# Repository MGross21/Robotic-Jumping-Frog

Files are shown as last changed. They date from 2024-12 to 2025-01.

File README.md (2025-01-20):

# Robotic Jumping Frog
*A Bio-Inspired Robotic System Aimed to Compare Physics Simulation and Physical Recreation*

*By Jacob Pisors and Michael Gross*

## Video Presentation

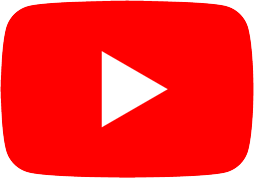
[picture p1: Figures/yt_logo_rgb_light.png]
See Here (https://www.youtube.com/embed/GysCEJ6NQpc)

\
`Click YouTube Logo to be Redirected`

## Project Overview

Continuing with the project's previous research, the team hopes to define the frog five-bar model in simulation using Mujoco, building off the kinematics. Then optimize the parameters for design, namely the joint stiffness, overall length, and various link lengths. Given this, the team will plan and fabricate the prototype using foldable robotics methods, and use then test it and capture the results. With that, an experimental validation will be complete and the team can analyze the results.

Specifically, the scope of this project is given the frog's inherent body mass, how can we reconfigure the link lengths and material stiffness of the five-bar mechanism, representative of rear frog legs, to determine the optimal vertical and horizontal propulsion during its jumping gait. The rationale for this decision is explained in part 2, where we optimized the design.

Simulation vs Prototype Final Video Results
___

### Part 1: Define the System Model

The model, as linked [here](frogModel.xml), allows for link lengths and joint stiffness to be changed easily by passing in the desired lengths. This will update the model and help when re-running the simulation many times as needed for optimization.

The team used [motor characterization](System_Model_Identification/MotorModel.ipynb) and [compliant beam analysis](System_Model_Identification/compliant_beam_analysis.ipynb) to determine the model parameters. 

Additionally in this step, considering the desire for a two-foot jumping gait, the team determined through the motor motor characterization and analysis that there was a physical constraint to the design of the controller and the max potential impulse. The minimum time in which we could use the full 180-degree motion of the servo was about 0.35 seconds which not only determined how fast the legs could move but how fast they could retract before landing.

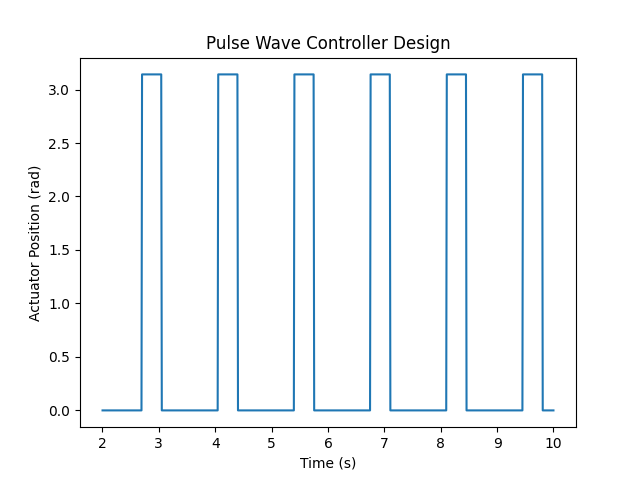
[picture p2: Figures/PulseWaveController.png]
PulseWaveController


___

### Part 2: Optimize your Design

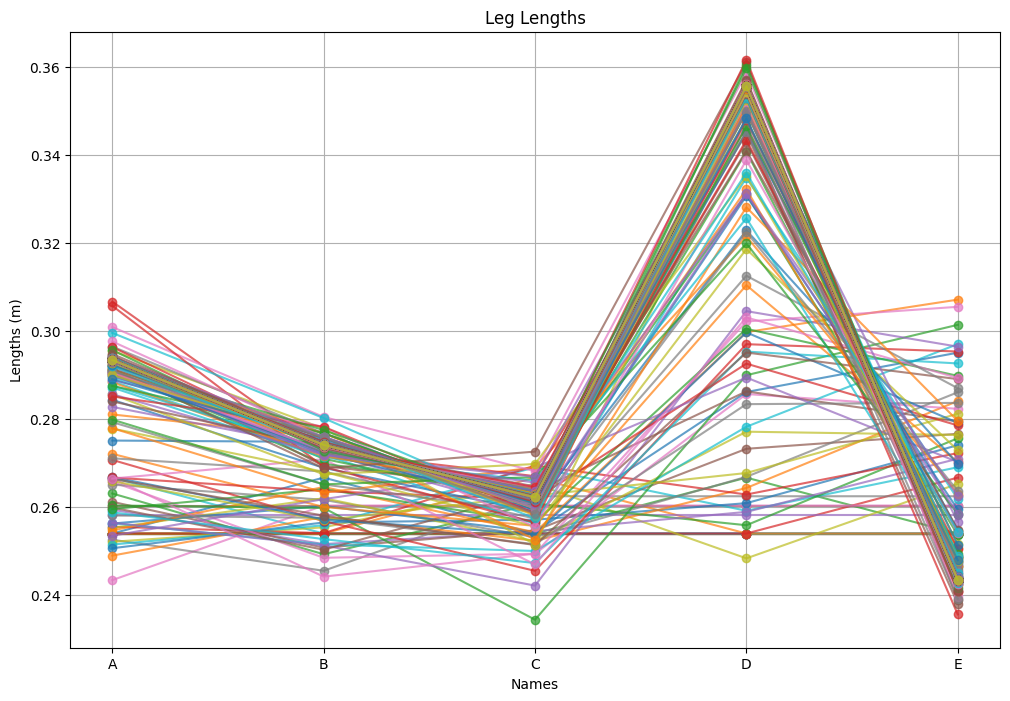
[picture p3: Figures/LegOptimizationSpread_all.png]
LegOptimizationSpread_all


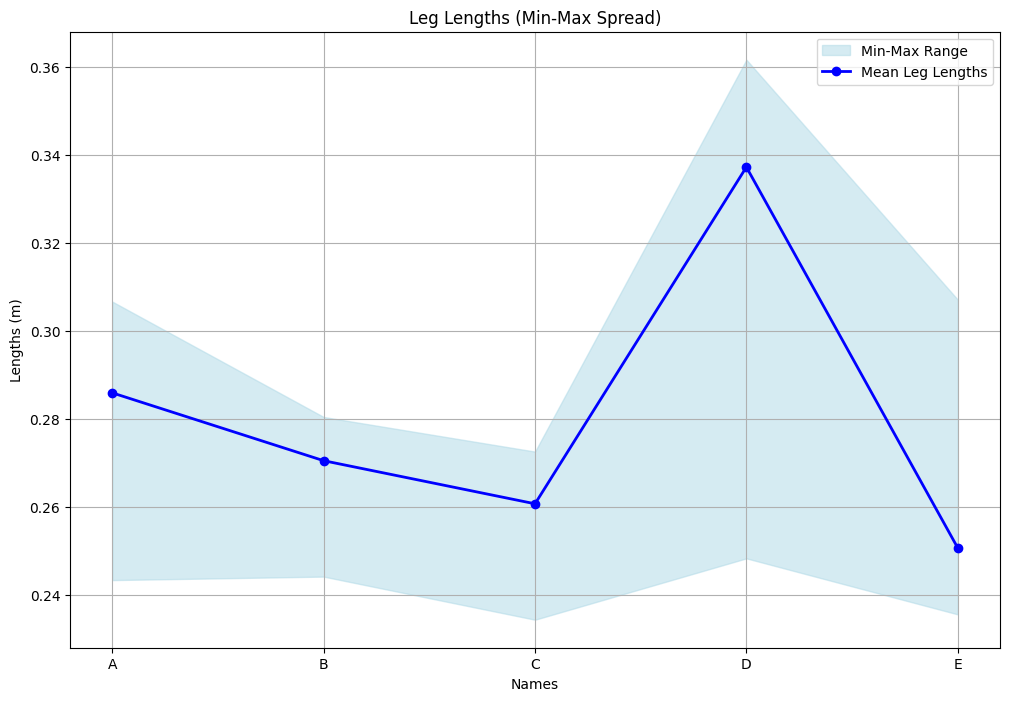
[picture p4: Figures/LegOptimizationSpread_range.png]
LegOptimizationSpread_range


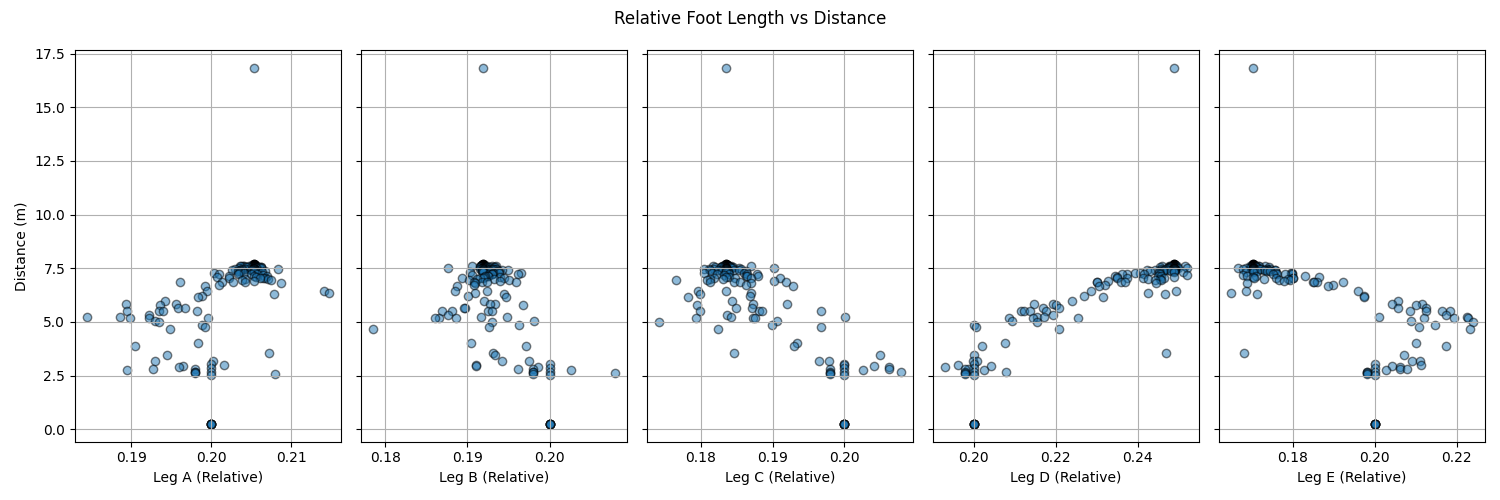
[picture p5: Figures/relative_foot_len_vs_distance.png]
relative_foot_len_vs_distance


#### Optimization of Link Lengths

The team noticed that the link length D, or the “foot” of the robot, had the largest variation of length in the optimization step, causing our team to investigate whether this meant the greatest impact on distance. Or rather, it was the most important factor of the five-bar when determining the jumping behavior of the frog. Thus, we decided to vary this parameter and analyze its effect.

For future manufacturing steps, the team also looked into the optimal stiffness and how the distance was affected. That can be seen in the figure below.

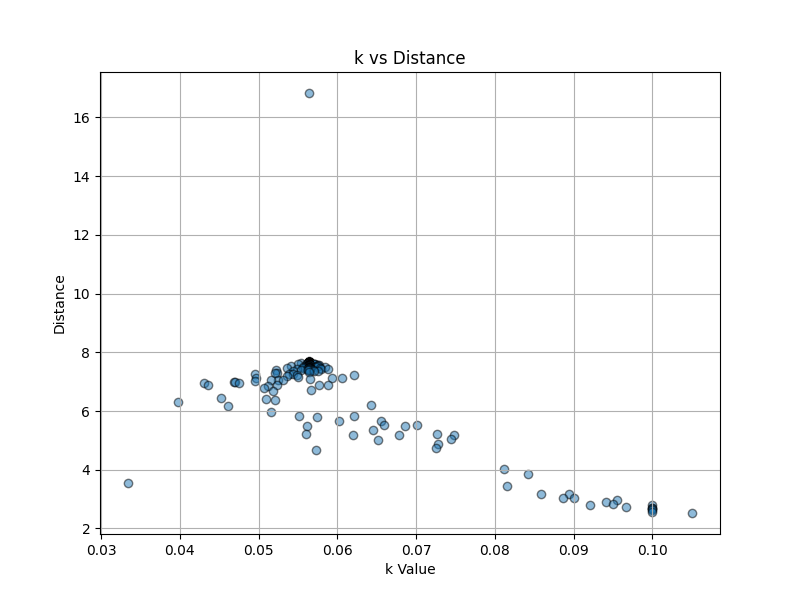
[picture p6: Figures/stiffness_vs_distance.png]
stiffness_vs_distance


To test this model, we developed a very modular, yet simple frog XML [simulation file](frogModel.xml). This allowed the team to change any parameter from frog leg lengths to segment mass. The design we went for was representative of the final physical structure, requiring a flat mounting point for electronics and compliant, skid-style front legs. The XML was dynamically regenerated using an XML template.

The metric that best describes the performance of the frog robot is the total distance traveled or the magnitude of the x and y distance. We wanted to prioritize this as it best represents the physical bio-inspired counterpart. Additionally, it prevents the simulation optimizer from biasing towards a sliding robot or a high-vertical jumping robot rather than a healthy balance between the two.

Despite adding the capability within our XML, the team opted to use the prismatic joint position and time derivative thereof: `qpos()` & `qvel()`. We made custom methods to make the process and access to such simulation variables easier.

The team used the `scipy.minimize.optimize()` function in Python which is a non-linear approach utilizing gradient descent. As shown above, in the scatter plot of each foot segment, we can see a convergence of ideal foot length segments given inter-variate relationships, and frog mass, among other variable influences. In addition to each leg segment per the jump distance, we also investigated the relationship between the front two leg segments, B+C, and the hind leg segments, D+E.

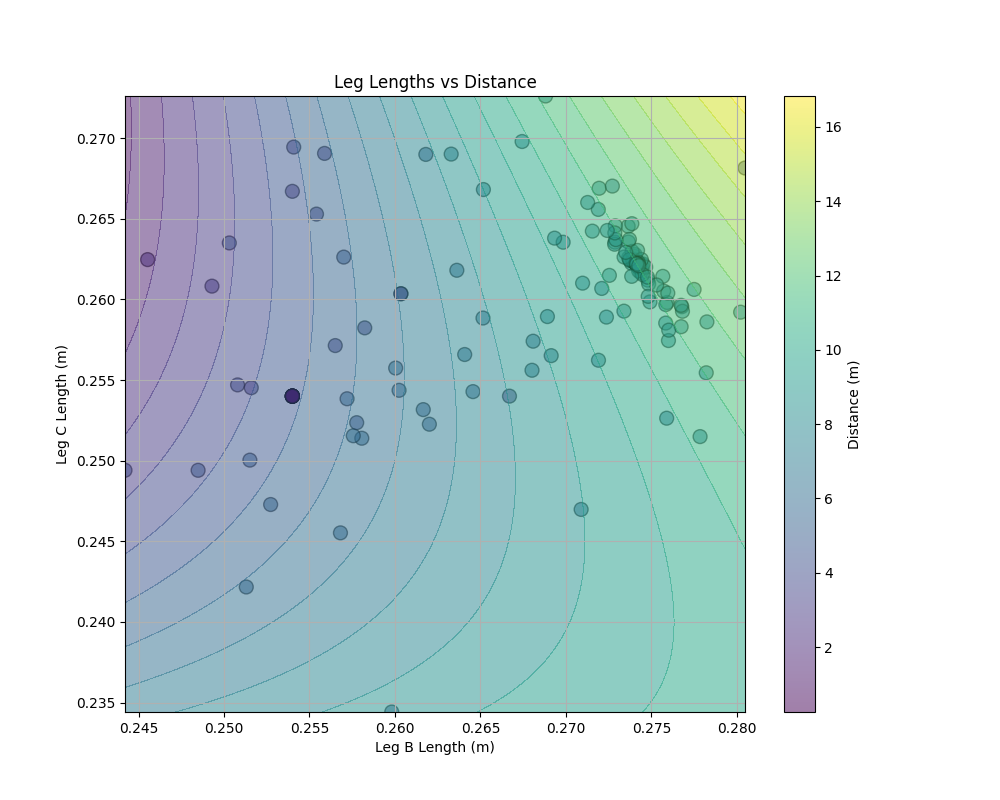
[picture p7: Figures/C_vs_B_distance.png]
C_vs_B_distance


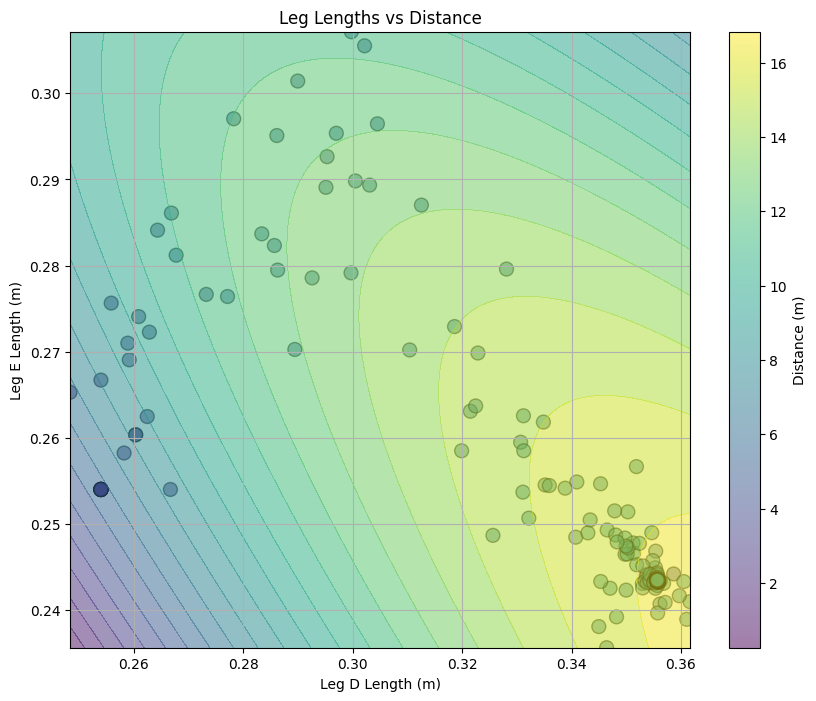
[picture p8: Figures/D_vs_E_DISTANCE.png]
D_vs_E_DISTANCE


Considering our earlier observance of how the variance of D had the largest impact on jump distance and how we originally suspected that to be the “foot” segment, we chose to vary that segment based on a percentage makeup of the full leg length.

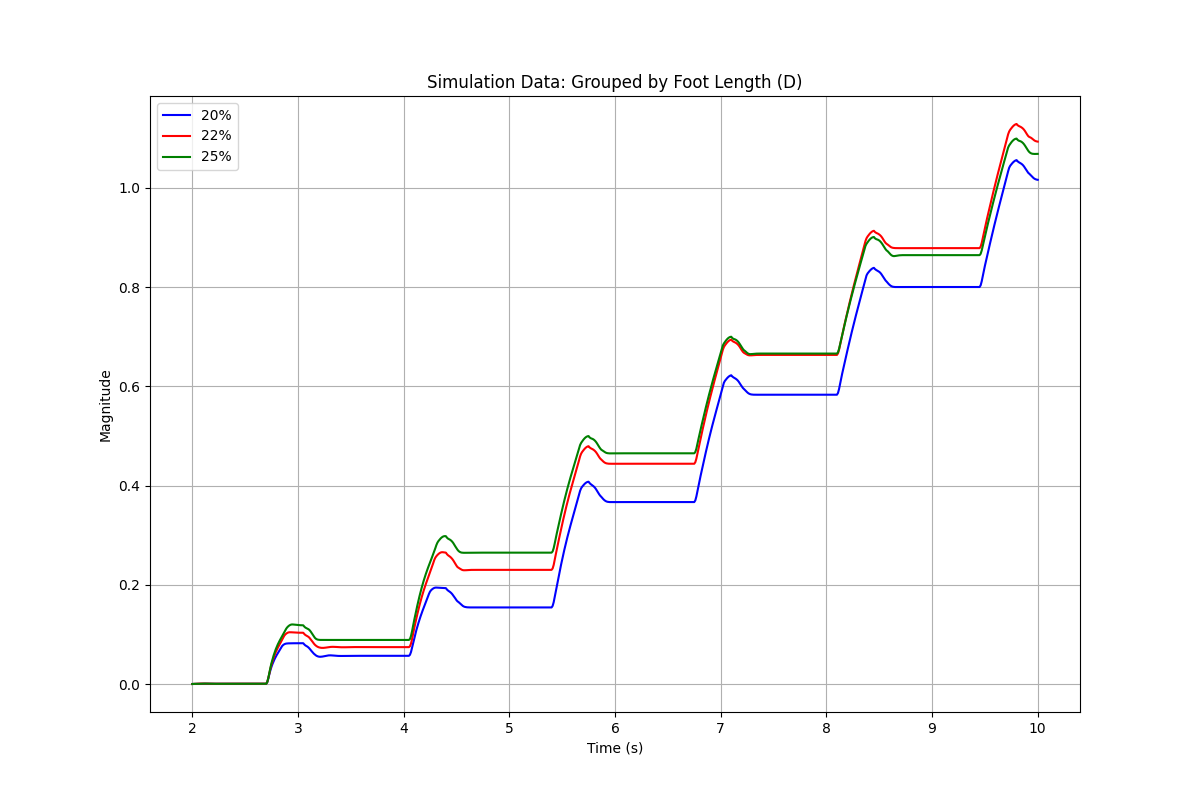
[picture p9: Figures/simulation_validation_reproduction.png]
simulation_validation_reproduction


To make a similar experiment, the team plans to make a program to change the link length of D whilst keeping the proportions mostly the same and the overall length the same. Swapping out legs and attaching a servo to segment B on each and making a frog body to keep it stable. More on this in the next sections.

___

### Part 3: Plan and Execute the Manufacturing

The mechanism that will be fabricated will be the five-bar mechanism that represents the frog's legs. This was done in LibreCAD, as seen in the figure below. Where the red line indicates the body and the blue lines indicate joints. The extra link at the end is a tab used for connecting the five bars.

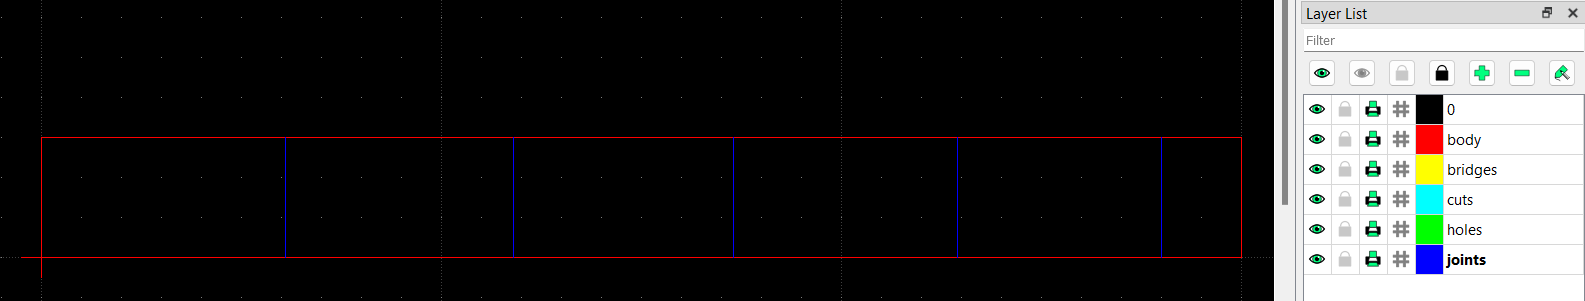
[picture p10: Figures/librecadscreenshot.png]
librecadscreenshot


The link lengths were influenced by the simulation. From the sim, the team knew we wanted to test out how link D, the "foot" affected the jump distance. However, from our simulation, we also gathered ideal proportions of the links for jumping. So, using those proportions, we found out how to dynamically adjust the percentage that links D relative to the overall length whilst keeping the proportions as similar as possible. So we could adjust the percentage we wanted link D to be in our [code](Frog_Model_Optimization.ipynb) and have it output where the joints should be in our model. Below is a figure comparing the percentages of link D we chose to study, based on our simulation that showed that as link D was a greater percentage (up to a certain point), jump performance should be improved.

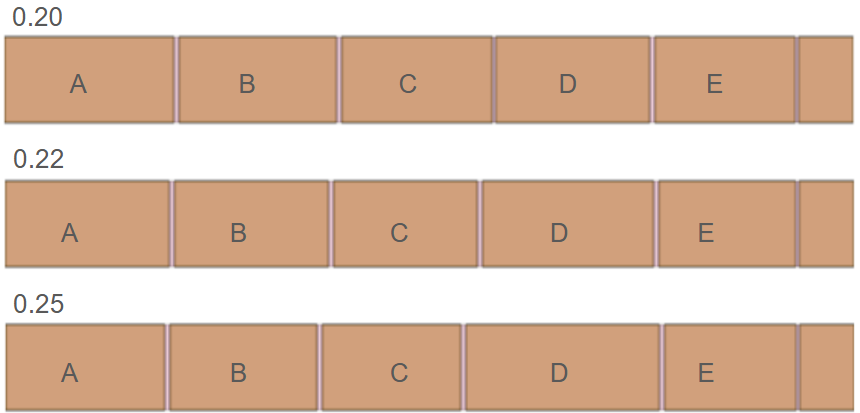
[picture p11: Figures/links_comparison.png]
links_comparison


This was manufactured using a five-layer approach, with the layers being rigid, adhesive, hinge, adhesive, and rigid respectively. Where the rigid layers represent the links, and are similar to the adhesive layer. The hinge layer is for the joints. These layers were derived from the original LibreCAD model and then adjusted with shapely and foldable_robotics libraries to produce dxf files that we could cut and laminate to make the final mechanism. See the jupyter notebook file for more details. The dxf files used are in the cut files folder on the GitHub page. See the figures below for a sample of what the cut files looked like and the final device.

finalcutpic

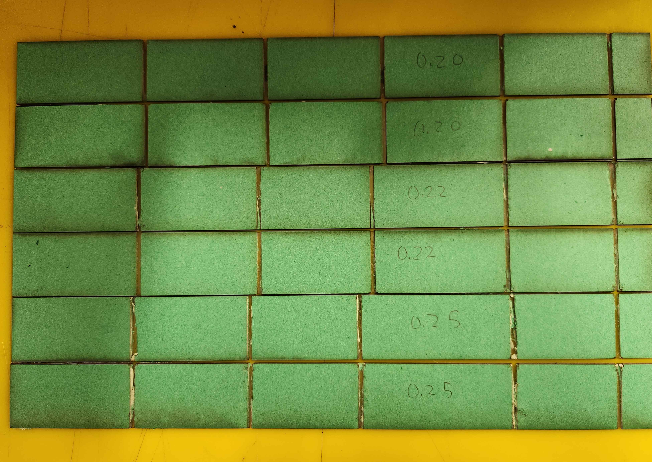
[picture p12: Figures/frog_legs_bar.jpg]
frog_legs_bar


With all the variants of the leg mechanism made, it was time for testing. First, the mechanism was folded into the five-bar. Then, since the frog needed to jump, we created a lightweight body frame out of cardboard. The servos were attached underneath and connected to the "B" bar from the side. The servos were connected to the body using a binder clip. We could also easily adjust the weight using binder clips. For the front leg of the robot, we used a passive leg with tuned stiffness from real testing to allow it to take some of the impacts of a jump and collapse like a real frog's front legs, with a slider on the bottom to reduce friction and rubber band to adjust stiffness. Rubber from cut strips of rubber bands were glued to the foot link to add friction between the previously smooth surface. Lastly, we realized we had not properly considered the weight of the mechanism about the torque of the servos, so to account for this we removed approximately 30 grams of weight using helium balloons. 

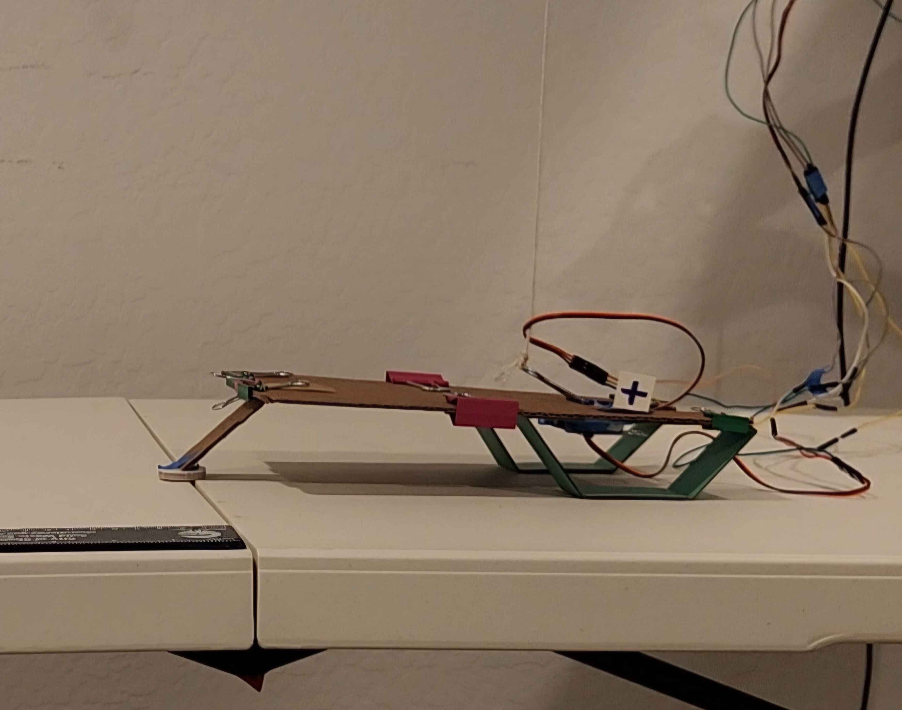
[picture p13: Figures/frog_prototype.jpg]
frog_prototype


For the electronics and code, the servos were wired up using long wires to allow for testing multiple jumps, and the ESP32 code was set to the same gait cycle as the simulation. Upon rebooting, the code would execute for 10 seconds, which equated to eight jumps. The hip motor control was timed to allow the gait to jump and then retract the legs while it was moving forward and "jumping." See the code [here](FrogJump-ESP32_Controller/main.py). The wires and ESP32 were held during testing to ensure they did not interfere with the frog. The IMU was not used due to the error from attempting to take the position from it being too large and accumulating too fast.

#### Recorded Behavior

During testing, it seemed that the 20% D leg length was the most consistent in distance and jump height. The 22% was relatively flat, and the 25% was inconsistent but looked to produce some of the highest jumps, but this did not correspond with the furthest distance. The furthest distances traveled were about three feet, and the highest jumps were only a few millimeters off the ground. See the figure below for the results which show (what they show). These results were from using motion tracking on the frog, where the marker was tracked by frames per second.

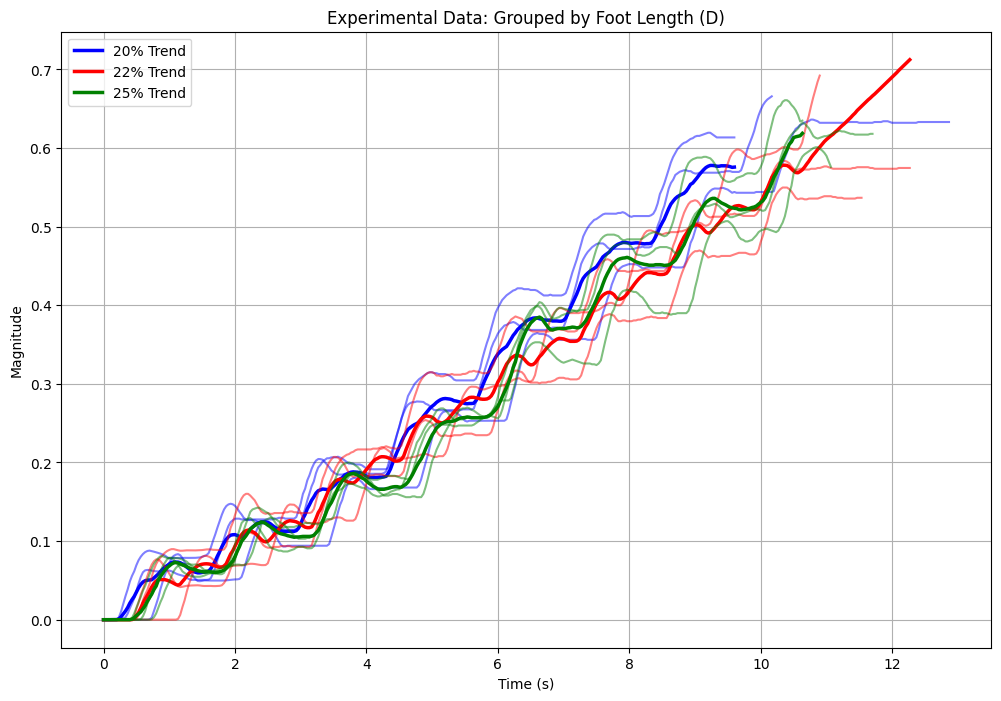
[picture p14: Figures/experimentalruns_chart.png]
experimentalruns_chart


*Real experimental data of each group. Three runs were done of each.*

The figure confirms a lot of the qualitative data. Where the 20% D segment outperformed. The 25%, with some relatively high spikes in magnitude, ultimately did not go as far as the others. The results were that the frog can hardly jump, though it can move forward through this gait. This is somewhat expected, though disappointing when considering the max speed and torque the servo motors could provide. A jump requires more of an impulse, way higher than that of walking motion - something the five-bar mechanism could not provide in its configuration.

It should be noted that during testing various problems could have accounted for this data. More on this in the Experimental Validation and Analysis section.
___

## Experimental Validation and Analysis

The figures below compare our simulated data group to the real-world results. Where we kept constant mass and dimensions in our simulation to real life to the best of our ability. The length of segment D was changed, as explained in optimization.

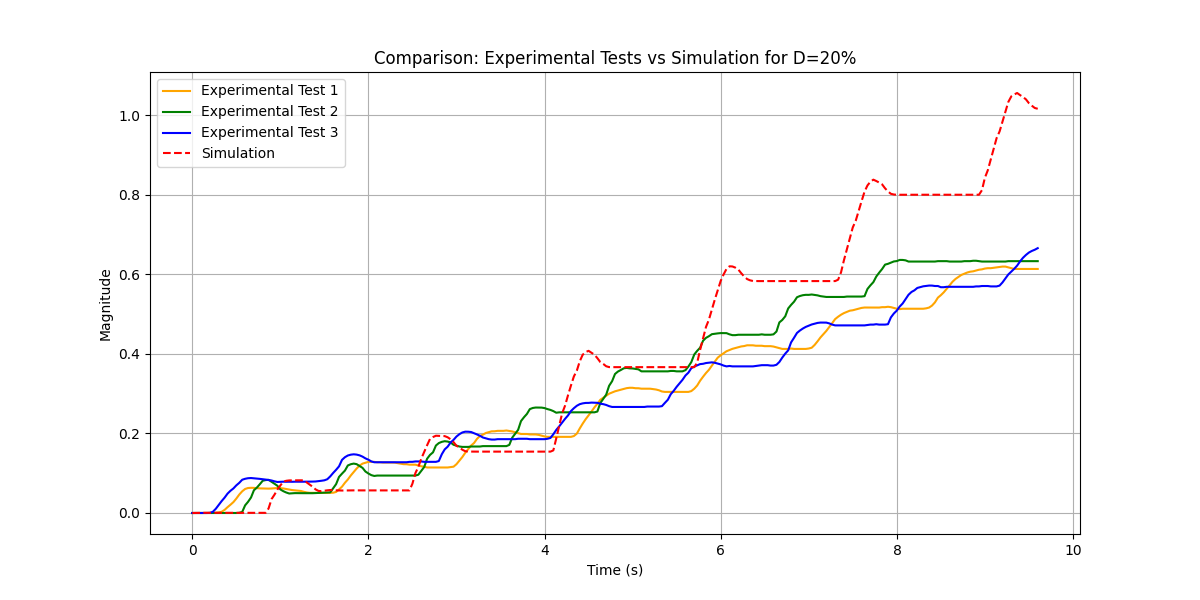
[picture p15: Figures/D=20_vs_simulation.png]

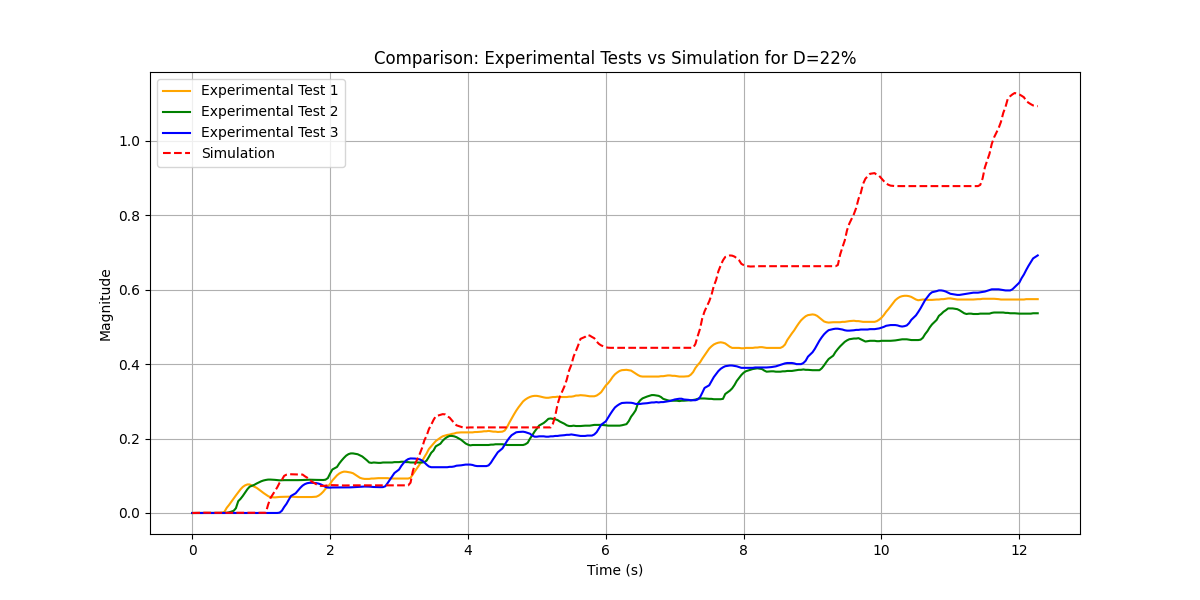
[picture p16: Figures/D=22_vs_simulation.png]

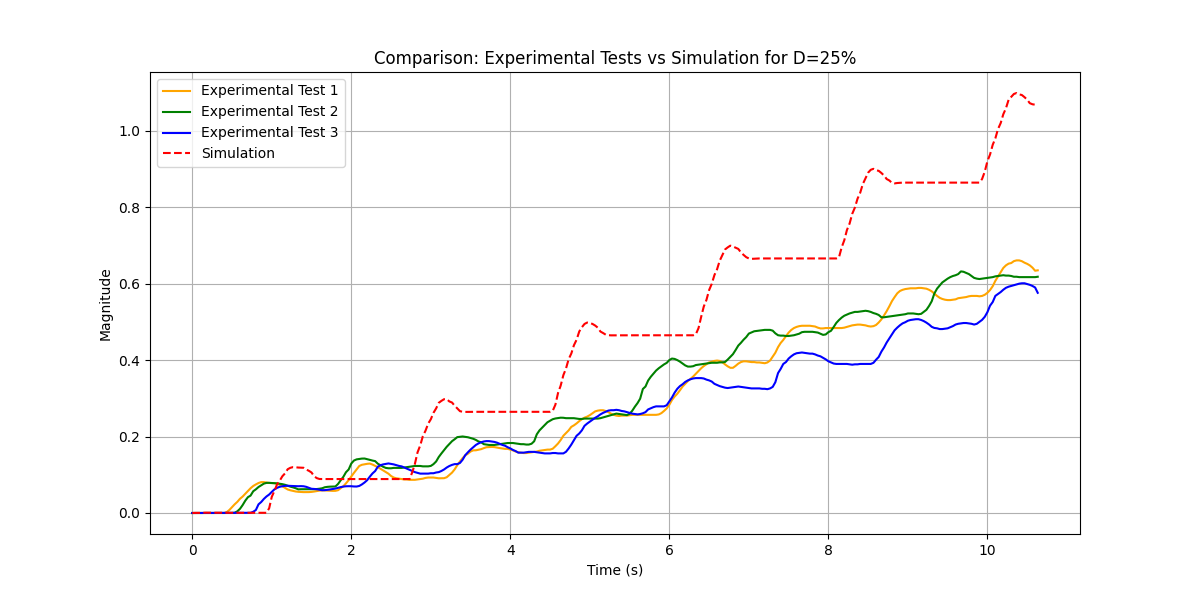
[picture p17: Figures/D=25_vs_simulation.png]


The data did not prove the hypothesis and simulation that the larger percentage of the foot segment would lead to a greater jumping distance. Rather, a refined balance based on the controller timing and foot trajectory is necessary to produce a greater jump. Also, the angle of the foot was not taken into account, which is a contributing factor.

Whilst the team attempted to use an IMU for data collection, the position, double derived from the acceleration, accumulated too much error too quickly and was not useful. Pivoting to using motion tracking software, Tracker, and a marker on the robot to collect the x and y positions about time. The data from this was exported via a .csv file and cleaned and compared to the simulation data. The small scale of the robot and changes could also have been a contributing factor to the results not being as clear as the simulation. Where changes in the small and delicate system can have unintended consequences. For example, some of the leading sources of error between the sim-to-real gap were friction and motor characteristics. Initially, the motors in the simulation were more powerful than they should have been. While we ended up changing them after characterization to be more accurate, they still underperformed in testing. Friction forces such as drag and the poor friction between the foot and surface also affected performance. Changing the surface could have improved this.

Furthermore, in the next version of this device, we would like to upgrade the servos and work more with the five-bar mechanism to add stiffness and have multiple servos on each leg so that the control can be better optimized for jumping and the stiffness can build and act as a spring.

___

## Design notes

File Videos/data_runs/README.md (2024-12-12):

Videos of the prototype robot

https://youtu.be/0vkdcDsntLY

https://youtu.be/EgqyHiKYC8w

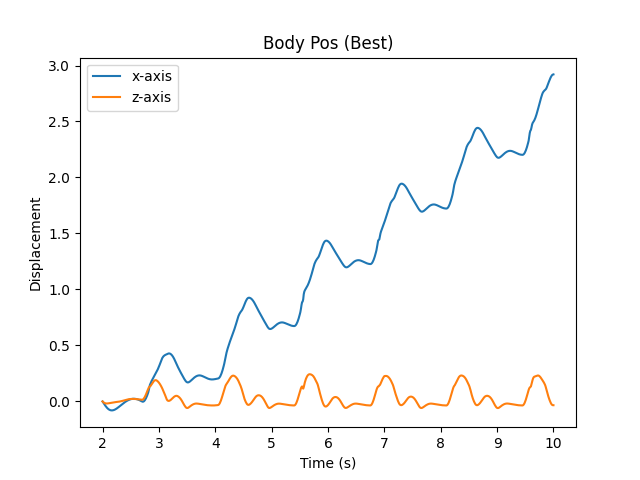
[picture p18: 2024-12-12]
Figures/Body Pos (Best).png

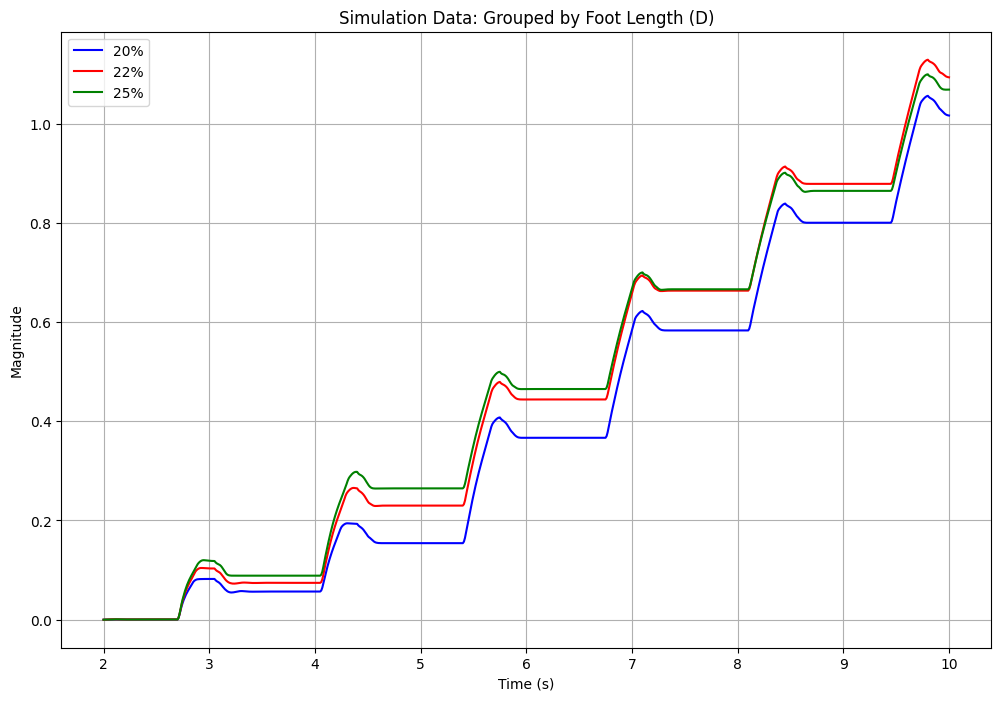
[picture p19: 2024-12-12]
Figures/simulation_comparison.png

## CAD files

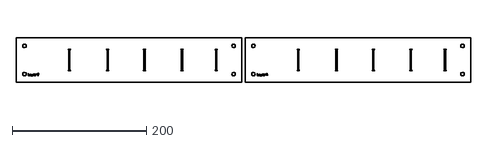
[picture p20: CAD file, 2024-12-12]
manufacturing/cut_files/0.20dxfiles/0.20_first_pass0.dxf
678.2 x 66.6

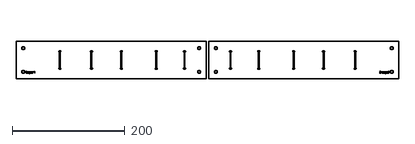
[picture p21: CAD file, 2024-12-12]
manufacturing/cut_files/0.22dxfiles/0.22_first_pass1.dxf
678.2 x 66.6

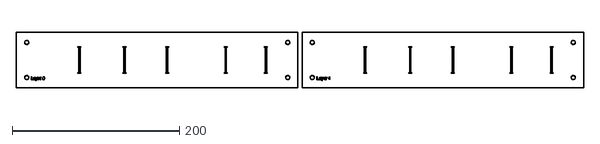
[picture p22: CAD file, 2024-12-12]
manufacturing/cut_files/0.25dxfiles/0.25_first_pass0.dxf
678.2 x 66.6

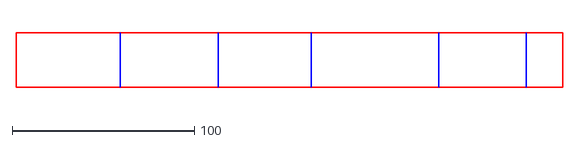
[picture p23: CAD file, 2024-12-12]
manufacturing/dxf_files/0.25lengthD.dxf
300.0 x 30.0

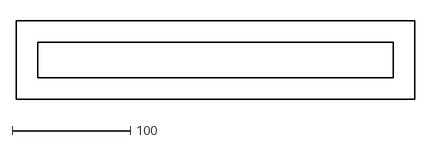
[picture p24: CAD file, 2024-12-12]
manufacturing/cut_files/0.20dxfiles/0.20_final_cut.dxf
336.6 x 66.6

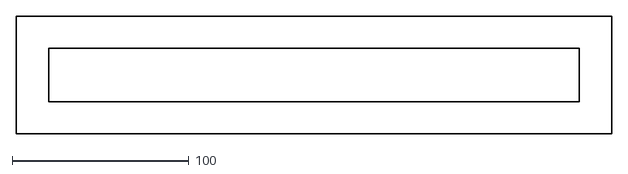
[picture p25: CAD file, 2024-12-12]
manufacturing/cut_files/0.22dxfiles/0.22_final_cut.dxf
336.6 x 66.6

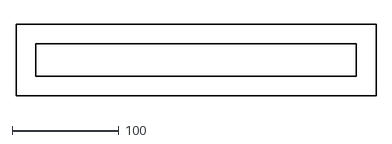
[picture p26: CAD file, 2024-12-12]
manufacturing/cut_files/0.25dxfiles/0.25_final_cut.dxf
336.6 x 66.6

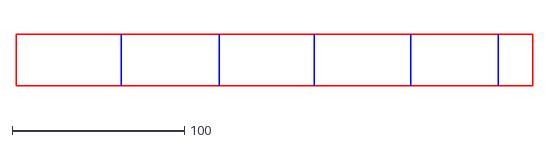
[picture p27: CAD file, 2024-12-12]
manufacturing/dxf_files/0.20lengthD.dxf
300.0 x 30.0

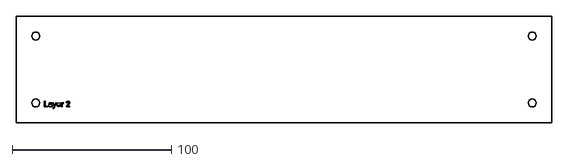
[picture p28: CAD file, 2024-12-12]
manufacturing/cut_files/0.20dxfiles/0.20_first_pass2.dxf
336.6 x 66.6

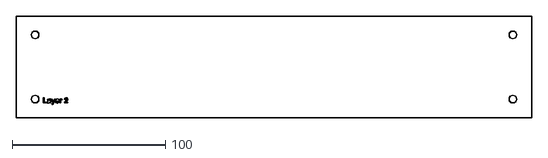
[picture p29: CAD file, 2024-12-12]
manufacturing/cut_files/0.22dxfiles/0.22_first_pass2.dxf
336.6 x 66.6

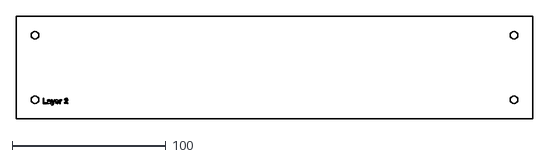
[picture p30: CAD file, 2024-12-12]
manufacturing/cut_files/0.25dxfiles/0.25_first_pass2.dxf
336.6 x 66.6

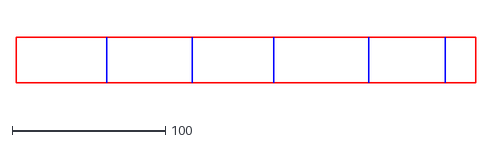
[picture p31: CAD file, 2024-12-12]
manufacturing/dxf_files/0.22lengthD.dxf
300.0 x 30.0

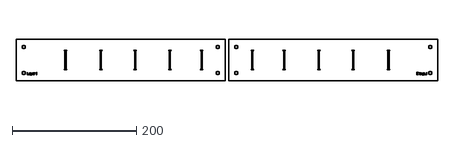
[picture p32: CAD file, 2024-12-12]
manufacturing/cut_files/0.20dxfiles/0.20_first_pass1.dxf
678.2 x 66.6

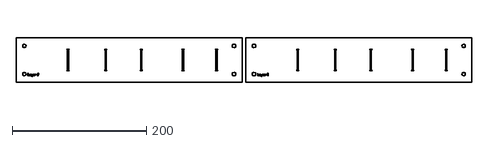
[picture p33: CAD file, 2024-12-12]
manufacturing/cut_files/0.22dxfiles/0.22_first_pass0.dxf
678.2 x 66.6

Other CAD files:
manufacturing/cut_files/0.25dxfiles/0.25_first_pass1.dxf

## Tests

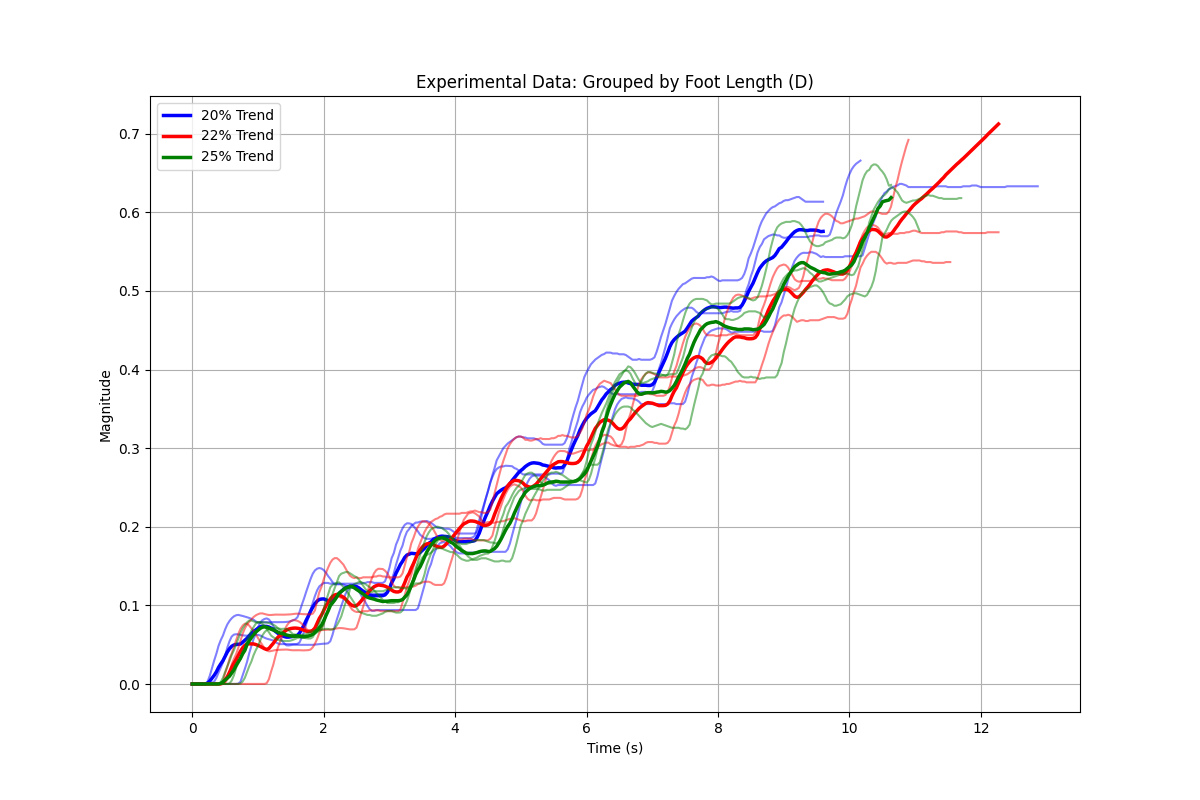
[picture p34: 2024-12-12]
Figures/experimental_grouped_trend_line.png

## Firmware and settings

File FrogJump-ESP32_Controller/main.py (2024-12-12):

# # main.py: Main program logic
# from bno08x_i2c import *
from boot import get_hardware
import time

# # Get hardware instances
i2c1, servo1, servo2, range_low1, range_high1, range_low2, range_high2 = get_hardware()

from machine import Pin, PWM
from time import sleep, ticks_ms, ticks_diff

frequency = 50
range_low1 = 50
range_high1 = 122

range_low2 = 28
range_high2 = 100

servo1 = PWM(Pin(13), freq=frequency)
servo2 = PWM(Pin(12), freq=frequency)

start_time = ticks_ms()

while ticks_diff(ticks_ms(), start_time) < 10000: 
    servo1.duty(range_high1)
    #sleep(0.09)
    servo2.duty(range_low2)     
    sleep(1)
    servo1.duty(range_low1)
    #sleep(0.09)
    servo2.duty(range_high2)  
    sleep(0.35)
    print("Cycle complete")

servo1.duty(range_high1)
servo2.duty(range_low2)
print("Finished")

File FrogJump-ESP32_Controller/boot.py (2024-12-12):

# boot.py: Hardware initialization and setup tasks
from machine import I2C, Pin, UART, PWM
import time

# I2C Configuration
I2C1_SDA = Pin(32)
I2C1_SCL = Pin(33)

i2c1 = I2C(1, scl=I2C1_SCL, sda=I2C1_SDA, freq=100000, timeout=200000)
print("I2C Device found at address: ", i2c1.scan(), "\n")

# Servo Configuration
frequency = 50
range_low1 =  50
range_high1 = 122

range_low2 =  28
range_high2 = 100
servo1 = PWM(Pin(13), freq=frequency)
servo2 = PWM(Pin(12), freq=frequency)

# Export variables for use in main.py
def get_hardware():
    return i2c1, servo1, servo2, range_low1, range_high1, range_low2, range_high2

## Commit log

2024-12-12 repo init
    [frog_11-28-2024_00-18-11.csv, run1_20.csv, run1_22.csv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]
2024-12-12 cut down jupyter. moved model to xml
2024-12-12 saved new figures. continued to cut down on main ipynb
2024-12-12 add images
    [servo_data_collection.yml]
2024-12-12 move manufacturing
    [0.20_final_cut.dxf, 0.20_first_pass0.dxf, 0.20_first_pass1.dxf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]
